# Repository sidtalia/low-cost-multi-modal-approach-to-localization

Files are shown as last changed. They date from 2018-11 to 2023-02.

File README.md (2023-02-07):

Associated paper: https://ieeexplore.ieee.org/abstract/document/8979000

If you find this work useful, please cite:
```
@inproceedings{talia2019multimodal,
  title={A multimodal approach for localization of Ackerman steering micro ground vehicles in bad GPS reception environments},
  author={Talia, Sidharth},
  booktitle={2019 3rd International Conference on Recent Developments in Control, Automation \& Power Engineering (RDCAPE)},
  pages={64--69},
  year={2019},
  organization={IEEE}
}
```

# Self-driving-car-STM-32

This project is the third iteration of my attempt at a mini self-driving car. It started as an imitation of the ArduRover project without all the fancy GUI. I started doing this practically on a dare, but quickly realized I absolutely enjoyed the point where cars met robotics. Personally, I am a petrolhead, but I also love making things work autonomously and this project feels like the perfect spot in the middle. While the title does say its a self driving car project, the focus is actually on aggressive driving. 



The above images show the first, second and third (current iteration) in that order. The first one had the connections hot-glued instead of soldered (yes). It has a come a long way since then.

The first and second versions were built on the Atmega328P and the third one on the STM32F103C8T6 (aka the 'blue pill'). In all these projects, my aim has been to keep the cost of the controller and hardware as low as possible. This does put a limitation on how much processing power I can have but that's really where all the fun is; to send a rocket to the moon with computational power less than that of a modern wristwatch.

Oh and by the way, only the rear wheels get power, i.e., its a rear-wheel-drive and rear-wheel-braking setup (imagine racing with a R.W.D car and using the hand brakes instead of normal brake pedals. Yikes!). This only makes the control problem more interesting.

Roadmap:
- [x] Outdoor relative localization (or odometry as most people like to call it)
- [x] Implement manual, partial manual and auto modes with failsafes
- [x] Trajectory generation and following
- [x] Preemptive braking to allow for faster speeds (Tested upto 8m/s on worn out tires. Will test again with new tires (normal medium soft compound)
- [x] Offline trajectory optimization given a set of waypoints (x,y) with a margin of adjustment and track width (WIP) 
- [ ] SONAR/LIDAR based obstacle avoidance for emergency braking (This part is taking a while because apparently cheap lidars don't work well in outdoor environments).
- [ ] Opponent detection using Object matching (may or may not be faster than object detection) (Jevois A33)
- [ ] Realtime trajectory update for overtaking (WIP)
- [ ] Designing overtaking policies (WIP. Currently learning about multi-agent navigation in UW's MUSHR project).

### About the project
The car can race around a track given a set of waypoints (already optimized for minimum laptimes). An offline optimizer does the job of optimization (Test Codes folder, waypoint.py). It can also act as a low level controller for higher level agents. The car can be given a point (X,Y,theta) relative to it's current location. Ideally, the higher level agent should give waypoints that do not force the car to go through an obstacle (that's kind of the point of having a higher level agent). The lower level controller takes care of figuring out the throttle and steering control for getting to a particular point.

### Odometry and localization
The localization is supposed to happen in open outdoor environments primarily using GPS data. I make the assumption that there is no exploitable feature in the environment. This is mostly because a system dependent on discernable features in the environment would not work as well in environments where there are none (CV techniques won't work in wide open parking lots). The user can always add their own way of localization and simply send the location data to the low level controller (the support for this will be incorporated if someone actually wants it). Most projects like these should be tested in wide open spaces for the sake of safety and so GPS based localization made the most sense as it is the most "generic" way of localization.



The odometry is obtained by fusing data from GPS, optical flow, IMU+compass and also from a simplistic model of the car's propulsion system, although the last method is kept as a last-resort under multiple sensor failures. The state estimator also exploits the non-holonomic constraints, using which it can get a speed measurement while the car is turning. Using multiple sources of information allows the car to operate with a high degree of accuracy (long term) when all the sensors are operating in peak condition and with an acceptable level of accuracy when one or two of the sensors are not in peak condition. The odometry assumes that the car is moving on a flat, horizontal plane (fair assumption for a car that has a ride height of 15 mm and is unlikely to go off-roading, however, the system can be extended to work on non-planar environments pretty easily).

Test for localization accuracy: https://youtu.be/GbBbyxaOqpI

Research paper for the same: https://ieeexplore.ieee.org/abstract/document/8979000
If this work is useful to you, please cite it! I'm a budding researcher and every citation goes a long way! :)

### Trajectory generation:
The trajectory is generated from given waypoints using parametric curves (3rd order Bezier curves). The motivation for me to use Bezier curves was to reduce computation and memory requirements as this codebase has to run on a tiny STM32F100 microcontroller.

### Waypoint generation:
The offline trajectory optimization takes in ordered waypoint regions, i.e., (X,Y, radius) as input arguments and finds the optimal (X, Y, heading) coordinates for the car to pass through such that the resulting trajectory would be optimal (what is considered "optimal" can be decided by the user). The cost function is comprised of a family of weighted potential fields (or sub-cost functions). These sub-cost functions are:

1) Total (absolute) curvature
2) The derivative of curvature
3) The second derivative of curvature
4) The overall length of the trajectory
5) C0 continuity between two consecutive sections
6) C2 continuity between two consecutive sections 
7) The sum of section-times (will be replaced with overall lap-time soon).

The weights for these sub-functions can be changed by the user. They are pre-multiplied by a normalizing factor so the weights can be adjusted relative to each other (a weight vector of [2,2,2,2] will have the same effect as a weight vector of [0.1,0.1,0.1,0.1]). The code for this is in /GCS/waypoint_optimizer.py. 



The next step is to make this less dependent on human input, like the work done here: https://github.com/a1k0n/cycloid (shoutout to a1k0n). 

### Control
The control is based on bezier curve(3rd order) based trajectory generation. There is also support for pre-emptive braking (more on that later).

The speed control uses an asymmetric non-linear controller. Big words? Here's a simpler explanation:
1) The car does not speed up and slow down in the same way; the response of the brakes is different from the response of the throttle, therefore there is asymmetry in the process being controlled.
2) The car does not speed up by the same amount for the same amount of change in throttle at different speeds, hence there is a non-linearity in the process being controlled.

(Note: I know that a system with a non-linear response is also by default asymmetric in response, but as I have specified above, the system is asymmetric beyond the general understanding of what it means to be asymmetric. The throttle controls the power to the wheels while the brake controls the force, in essence the system controls 2 completely different variables, leading to an asymmetric response.)

This means that in order to control the speed, I'd need a controller that compensates for both these problems and hence the big-words.
The steering control is an open + closed loop progressive P controller (progressive as in the gain increases with the error, like in a progressive spring). The combination of these 2 controllers allows the car to remain under control for the most part even without preemptive braking.

The control system can update the friction coefficient of the surface if it detects that the car is sliding when turning (by using optical flow data), and if it does enter a slide, it can handle itself ;)
GifMaker_20190831155907193

The system is also capable of preemptive braking, i.e., slowing down before the turn(as done in racing) instead of slowing down while turning.
Video link for preemptive braking :  https://www.youtube.com/watch?v=Ko5H_G4eCLo 
#### how preemptive braking is implemented: 
The car has a trajectory, it then finds the point of maximum curvature along that trajectory (upto the next checkpoint or waypoint) and determines maximum allowable speed for that curvature with some margin. The car then determines whether it should start slowing down for that point or not, on the basis of the deceleration required to hit that speed at that point. A more detailed discussion was done here (scroll down to the 5th last post which includes hand written notes): https://github.com/a1k0n/cycloid/pull/3

### Vision component: 
I have just started with computer vision please wait a couple of years.

### Ground control system and V2V communications:
The previous iterations did not have a GCS. This made debugging extremely hard as there wasn't an option of data recording or viewing the internal state of the controller in real time. The GCS in this work has the bare minimum features needed for debugging and is not on par with GCS's like Missionplanner or Qgroundcontrol, however, it gets the job done. The GCS allows me to record data that I could use for debugging as well as for finding flaws in the system. It can plot the position data from the car in real time.

The car is equipped with an Xbee pro (2.4GHz) and so is the GCS (GCS here can be your laptop). The actual purpose of the Xbee was not just for communication with the GCS for debugging and monitoring, but rather to allow multiple agents to communicate with each other, meaning that the car is V2X ready from the hardware's point of view. I got the inspiration to do this from a project I did last year under Celestini Program India at IIT-Delhi where I worked on ADAS coupled with V2V communication: https://github.com/Celestini-Lucifer/ADAS

# Note for potential users : 
The car will not operate without a GCS by default. This is for safety purposes and not for the sake of functionality. If the car were to operate without a GCS connection and only be in control of the user via radio control, there would be a single point of failure in communications. Adding the GCS-compulsion gives the system 2 independent points of failure. This also compulsorily limits the range of operation (which depends on the kind of transceiver used. For xbee pros, this range is ~80 meters, which is more than enough for doing experiments with a 1/10 scale car.)

The system has multiple failsafes (note that the car can be operated in auto modes without the transmitter, but it is advised to always keep a transmitter with you as a failsafe).
1) If the car goes outside the range of the GCS (Xbee, ~80 meters) the car will come to a halt. If the user wants to recover it, they have to move a 3 position switch on their Flysky Transmitter to the middle position for manual control (refer to the hardware folder for BOM). 
2) If the main controller (stm32f103c8t6) fails and stops producing appropriate pwm signals for the esc and servo, the secondary controller will take over and relay the control signals coming from the receiver directly to the esc and motor.
3) If the user feels that the main controller is misbehaving or not working as intended, they can flip switch D on their flysky fs-i6 (switch D on channel 6) to force the secondary controller to relay control signals directly from the receiver to the esc and motor.

## Photos of this project : 




## Building the project (in progress): 

(will update this as I build this project)

For the hardware specifications (including wiring specifications), 3d print files as well as 2 d drawings, go into the "hardware folder". 

For the back end libraries, go into the "libraries folder".

1) You will need : Arduino IDE (1.6.13 or better)

2) You will have to download the hardware files from : https://drive.google.com/file/d/1j8or7khmo2Z-QlrW-FHwhAybPbwVp9Ex/view?usp=sharing (its a slightly modified version of the original fork, I don't actually remember what changes I made but somehow the code after compilation takes 5 kB less memory) and unzip/extract it inside the "Arduino/hardware folder. You will also need to install the cortex M3 SAM board package in arduino, which can be installed easily through the boards manager in arduino IDE. Use this video for reference, the step of cloning the STM32 repository is replaced by downloading the zip and the rest remains the same : https://www.youtube.com/watch?v=MLEQk73zJoU&t=295s

The 'libraries folder' needs to go inside Arduino/libraries. The ino files need to go to wherever you store your sketches. Place the GCS folder where you keep your python files. The Baphomet code is for an Arduino Pro-Mini (5V, 16Mhz) and the Lucifer code is for the STM32F103c8t6. In the upload settings, set the CPU speed to overclocked (128Mhz) and upload method to serial.

### additional steps for Linux
Assuming you already have a functional installation of arduino (see here: https://www.arduino.cc/en/guide/linux )
You will probably face something that looks like this the first time you try to upload :
```
...../hardware/Arduino_STM32-master/tools/linux/serial_upload : error 13: Permission denied
```
just execute the following:
```
cd path/to/hardware/Arduino_STM32-master/tools/linux
sudo chmod +x *
```
and from within the same directory (path/to/hardware/Arduino_STM32-master/tools/linux)
```
cd stm32flash
sudo chmod +x *
```
now restart the arduino IDE and try uploading the code

### Common upload error:
```
Failed to init device.
stm32flash Arduino_STM32_0.9

http://github.com/rogerclarkmelbourne/arduino_stm32

Using Parser : Raw BINARY
Interface serial_posix: 115200 8E1

An error occurred while uploading the sketch
```
This happens when you forget to reset the stm32f103c8t6 (you have to push the reset button before the upload).
Again, watch this video for initial steps for stm32 bluepill https://www.youtube.com/watch?v=MLEQk73zJoU&t=295s

3) You will need Python
Python dependencies : 
Matplotlib,numpy, pyserial,scikit-learn :
```
pip3 install matplotlib
pip3 install numpy 
pip3 install pyserial
pip3 install scikit-learn
```

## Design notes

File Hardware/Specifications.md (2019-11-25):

# Hardware Specifications for this project

## The car : 
1) HPI sprint 2 (why? its a good balance between price and quality). I would suggest the "All aluminium upgrade".

2) ESC and motor : you're free to chose any ESC and motor combination but I like to run a 120 A ESC (hobbywing) and a (I use speedpassion but you can use any) 3500 kv sensored motor. (if you run the exact same hardware then you don't have to change a thing in the code).
3) Steering servo : SAVOX SC-1251MG . (any servo with equivalent or better torque and speed will work just fine. Any slower and you might face problems with oversteer).
4) Spur and pinion : 31 teeth pinion and 80-81 teeth spur (48 pitch both). if you use a different gearing ratio you'll have to calculate the maximum speed for your setup and put that number in the "CAR.h" file inside "libraries".
5) Drivetrain layout : RWD (this is to make space for the autopilot)
6) Suspension :
    1) Springs and dampers : standard HPI sprint 2 springs with 300 cst silicon oil all around.
    2) Steering geometry : 1 degree TOE-IN. (for stability at speeds). mount the steering links on the outer holes of the steering arms.
    3) Camber : Front = 0.5 or 0 degrees (Front end doesn't need that much camber). Rear = 2 degrees.
    4) Ride height : 25 mm all around. Think of this car as more of a road-rally sort of thing than a pure-bred racer.
7) Battery : 5000-6000 mAh 2S lipo. C rating may or may not matter depending upon your use case. I use 70C batteries from turnigy trackstar.

## The autopilot : 
1) The designs (obviously)
2) 1 x STM32F103C8T6 (if you get the CBT6 that works too) and 1 x Pro mini.
3) 1 x MPU9250.
4) 1 x ADNS3080 optical flow sensor.
5) 1 x Ublox M8N GPS (no config required, the code will do the config automatically for you).
6) 1 x Jevois A33 (optional) and a usb mini-b male adapter.
7) 2 x Xbee Pro with Xbee pro adapter (one for the car and one for your computer).
8) 1 x pwm to ppm converter (like the one used for Ardupilot).
9) 1 x Flysky Fs-i6 (or equivalent). Put switches C and D on channels 5 and 6
10) 1 x 5V/5A BEC (the one that you get from bang-good is just fine. It can actually only handle 3A without a voltage sag, but you can push it to 5. We won't actually need 5 A at all. We'll need ~1-1.2 A (this includes the current consumed by the jevois camera. If you're not using the jevois camera, the current consumption will be much lower, however I would still recommend using a separate BEC).
11) 4 x LEDs taken out from a computer mouse (please do not use a standard red LED. Just take the LED out from an old mouse. 
12) 1 x dot board/Zero pcb, single core wires, solder, male headers.
13) I might add more things for obstacle avoidance later. Right now I m considering the use of the camera itself to detect obstacles or run image segmentation

# Putting it together : (images will be up soon)
1) The chassis and chassis brace drawings are .dwg files because it has no 3d features and you can do a cnc(1.5 mm offset) cut. If someone asks for it I will upload an stl file if you want to 3d print it
2) The LED holder sits on top of the chassis above the slot. The holes have been cut into the chassis.
3) the chassis brace has holes for mounting the container base. mount the container on the chassis brace before adding any components to the autopilot.
4) the MPU is to be situated at the converging end of the container. The optical flow is placed in the raised slot. The GPS is placed on the container top behind the jevois camera.
5) the xbee is situated near the motor, so is the BEC and the pro mini.
6) The MPU is attached to pins B6 (SCL), B7 (SDA).
7) The Optical flow is attached to pins PA4 (NSS) PA5 (SCK) PA6 (MISO) PA7 (MOSI) PB0 (RESET)
8) The GPS is attached to PA2 (Tx, Rx of gps connected here) PA3 (Rx, Tx of gps connected here)
9) The Xbee is connected to PA9, PA10. Create a 6 pin male header that can accept an FTDI converter and connect the Xbee (and only the xbee) with jumper wires that can be removed later).
10) The Jevois is connected to pins PB11 (white wire), PB10 (yellow wire).
11) The extend a wire from pin PA8, PA11 to pins 3 and 4 of pro mini. These are servo and ESC wires.
12) Connect the PPM encoder to pin 9 of pro mini. solder a wire from PA0 to pin 9 of pro mini.

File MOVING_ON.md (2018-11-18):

# Why I moved on from the Arduino Pro Mini:

## Why improve the hardware?

Problems with Arduino Pro Mini:

1) Not enough UART ports (required for communication with GCS and a higher level system like idk a raspi or a jevois camera)

2) Not enough processing speed to maintain the same 400Hz state-estimation frequency with any added features (like sensor health checks). I was shaving off like 10-15 us per function minimum just to meet the requirements (although this did force me to come up with rather ingenious approximations which I have carried over to this project, so if you use my "math" functions (in the SIDMATH.h header) you can forget worrying about execution time of your algorithms- Its not a full blown math library because it isn't meant to be. It just includes some functions that I used very often like sin and cos my approximations are pretty close and have a worst case execution time which is 1/3rd (if i remember correctly) of the time taken by arduino's sin and cos. ).

Problems with previous layout of hardware:

1) The optical flow sensor was outside of the boundary of the car(behind the car) this caused there to be an unwanted cg offset + ugliness. The optical flow sensor now sits at the center of the car (at the cost of front wheel power. The car is now RWD).

2) Everything was connected by jumper wires. Yes. Really. In the new version, everything is soldered directly. 

Problem with previous hardware in general (this doesn't come under the above 2 categories) : 

1) The last and final crash of my previous iteration happened on July 22nd 8:30 AM. It happened because the MPU got disconnected mid-communications, which locked up the I2C line, producing a race-around condition. Due to this, the car could no longer be sent into a failsafe as it had gone into a lockout state. The car went at 7 m/s into a wall at an oblique angle, taking out the right front suspension.
For this reason I decided to put 10k resistors between SCL,SDA and VCC to prevent the race-around condition and instead of having just the main controller, have a slave controller that acts as a gateway between the car's hardware and the main controller, so that in case the main controller goes haywire, the slave controller can still shut the car down. How do I know this slave controller won't go into some lockout mode of it's own? I have tested the back end for it over 2 years and it has never failed (since it only uses interrupts and servo library and nothing else). It's sole job is to make sure that the car never goes completely out of control. (I am still on the fence about this though).

So whats the alternative? the STM32F103C8T6 (surprise surprise!) (a.k.a. the blue pill). The blue pill has 3 UARTs, 2 SPIs and 2 I2Cs (although I only use 1 I2C and 1 SPI port in this project, its nice to have options), 20kb of sram, 64 kb of flash memory (compared to 2 kb of sram and 32 kb of flash memory on mini pro), and a clock speed of 128MHz (after overclocking, which can be done from within the arduino IDE itself). Going from a Pro mini to the blue pill feels like going from a handgun to a bazooka.

Why improve the code? 
The right question would be, why not? The previous version had certain (kidding, a lot of) flaws like lack of modularity (each sub-module should be able to function somewhat on it's own and not be dependent on some other module entirely. If you look at my previous code, just about all variables are global. It gets hard even on the person who created it after a while (this is why object oriented programming is used kids) ) as well as misplaced functionalities (like incrementing waypoint index in the code block that is supposed to control the steering and throttle. Yes. Really. (cut me some slack I m still learning) ). 

In this version, I wrote back end libraries for just about everything (FYI this is my first time writing back end libraries) from IMU to the communication systems, so that I could divide things into sub-modules. This greatly cleans up the main code (though it's still not that clean). However, everything related to AHRS, from getting sensor data to calculating AHRS happens in the same library so that all the helper functions that could be used are in the same file.

If you know how to write code for a GCS in python, please create an issue and let me know, I need some help there. I can't seem to integrate google maps into this. Till then, Waypoints will be marked by driving the car to those waypoints in manual mode.

## Have I forsaken Arduino? 
No. The code is still compiled by the Arduino IDE. The main code that runs the car is still written in Arduino IDE (bite me). Why not just work with pixhawk (Ardupilot)? 

1) I am too dumb to understand what they're doing there. I am just not up there yet. So its better that I do not fiddle with things I do not understand.

2) I am trying to learn these things on my own. If I use the Ardupilot backend I will never really understand how these things work and what you need to take care of (corner cases, exceptions etc). 

3) If I have my own system, its easier for me to integrate new things into it since I don't have to comply to standards set by someone else. While standards are very useful at the professional level, they can slow down the process of testing and between my undergrad studies, academic projects, research papers and this, I do not have the time to go through these things like a professional.

4) If you wanna create a project using arduino supported mcus, you install the Arduino IDE and maybe some back end support (like back end support for STM32 controllers) which is also downloaded from within the Arduino IDE. Its super simple and you can get started with doing actual work. If you wanna create a project using pixhawk and you're on Windows, may god help you. 

Basically we need something like Multi-Wii but for r/c race cars instead of drones and we need it to be somewhat competitive against the apm rover. We also need it to be a bit more focused on racing, which means a bit more focus on the driving dynamics of the car (which AFAIK the apm does not really have since they simply minimize the angle difference between the direction where they wanna go and where they are going right now, which is fine and even required for WP missions but for racing you need the car to follow a smooth trajectory).

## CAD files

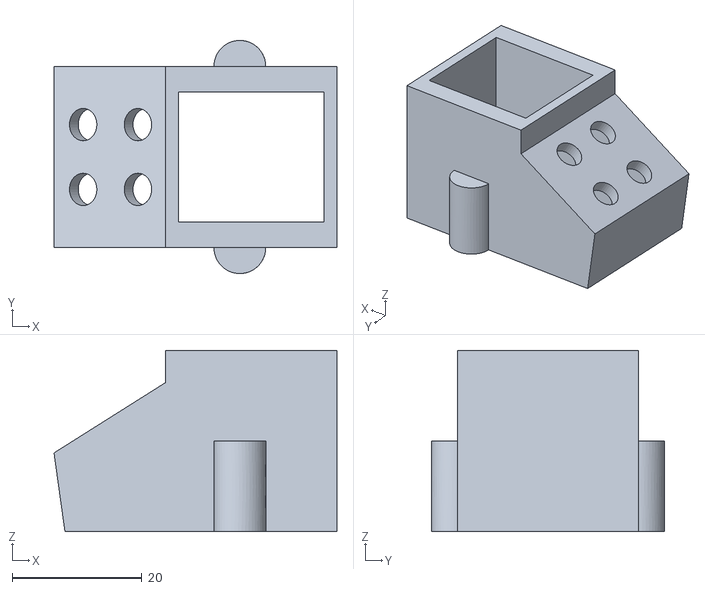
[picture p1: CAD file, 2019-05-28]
Hardware/LED_holder_proto_4.stl
43.7 x 36.0 x 28.0

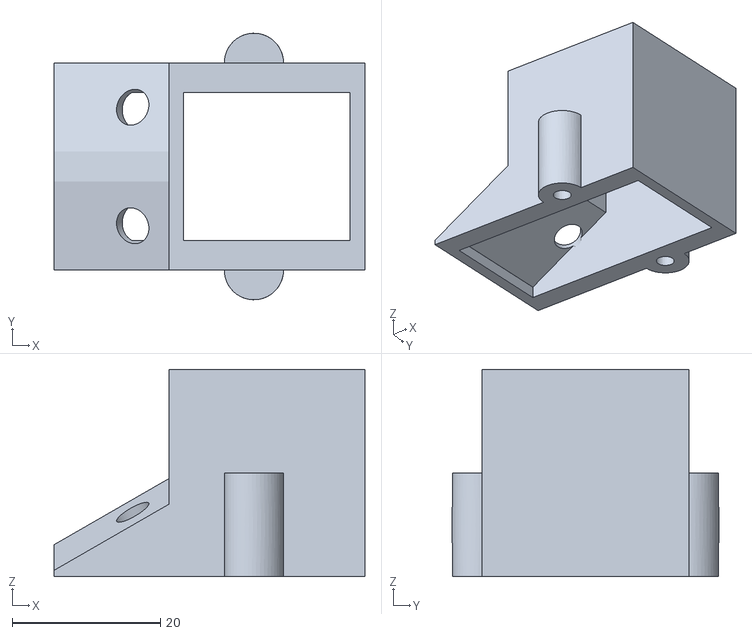
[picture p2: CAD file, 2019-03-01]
Hardware/LED_holder_new.stl
42.0 x 36.0 x 28.0

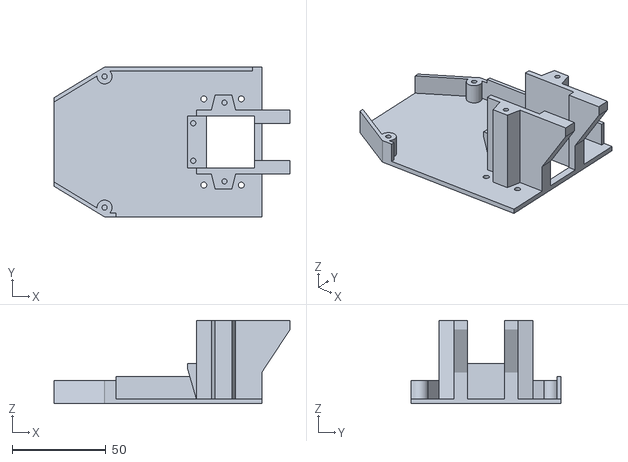
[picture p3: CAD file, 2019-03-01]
Hardware/container_base_new.stl
126.0 x 80.0 x 44.5

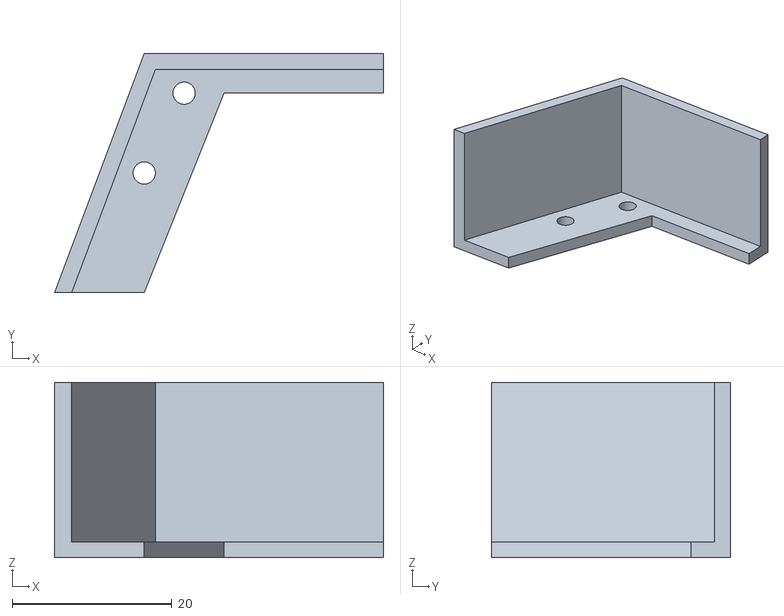
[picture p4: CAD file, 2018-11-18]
Hardware/Dust_gaurd_right.stl
41.2 x 30.0 x 22.0

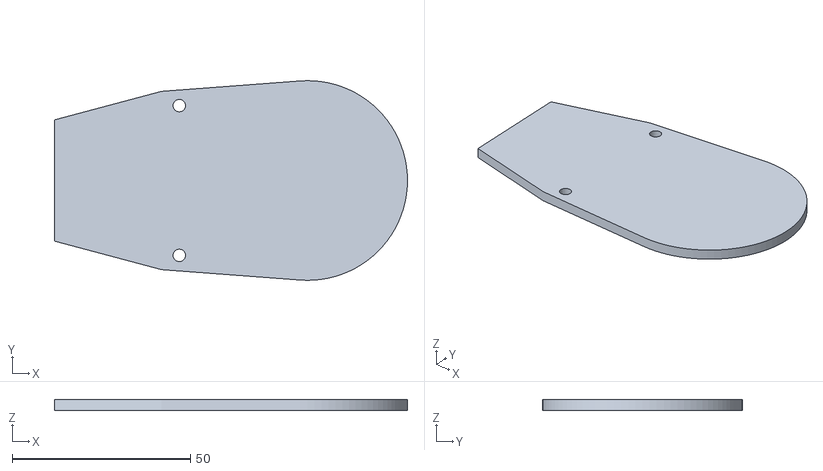
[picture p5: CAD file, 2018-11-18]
Hardware/container_jevois_gps.stl
99.0 x 56.0 x 3.00

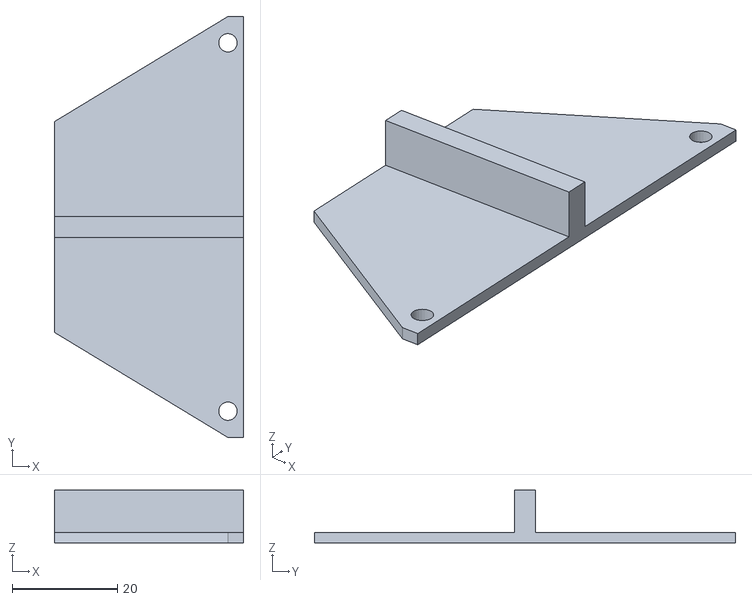
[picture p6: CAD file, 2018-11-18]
Hardware/container_top.stl
36.0 x 80.0 x 10.0

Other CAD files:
Hardware/chassis_design_updated_7_Aug_2019.dwg
Hardware/Dust_gaurd_left.stl
Hardware/chassis_brace.dwg
Hardware/modified_chassis_New.dwg

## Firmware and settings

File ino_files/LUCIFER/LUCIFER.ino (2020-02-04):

//You might observe some inconsistency between tabs and spaces between arduino code and the header file code.
//If that is a problem for you then you are free to edit the code yourself. I don't have the time to be concerned 
//with formatting as long as the code remains understandable.

//choose the 128MHz overclocked setting for compilation.

//If you want to cross check the time taken by any function, here is some help:
//in floating point, each multiplication takes 0.61us, each addition/subtraction takes 0.481 us, each division 2.14us
//in integer, divide the above numbers by 2 (roughly speaking). This gives a decent estimate of execution time. 
//The cycle time is constrained to 2500us. While its possible to run it down to 1250us without breaking a sweat, it would sacrifice system safety checks
//and re-initialization processes (say for example the MPU is somehow shut-off by chance. it takes about 470 us to re-initialize it).
#include"MPU9150.h"
#include"OPFLOW.h"
#include"GPS_NAV_PVT.h"
#include"MEMORY.h"
#include"INOUT.h"
#include"SIDMATH.h"
#include"COMS.h"
#include"STATE.h"
#include"CAR.h"
#include"PARAMS.h"
#include"TRAJECTORY.h"
#include"COMPANION.h"//CHANGED

MPU9150 marg;
OPFLOW opticalFlow;
GPS gps;
STATE car;
GCS gcs;
trajectory track;
controller control;
JEVOIS jevois; //CHANGED

bool GPS_FIX;
byte MODE = MODE_STANDBY;
byte message;
float inputs[8];
int16_t num_waypoints=0;
int16_t point = 0;
int16_t sentinel = 0;
bool circuit = false; //
bool car_ready = false;
float dest_X,dest_Y,slope;

coordinates *c;

void setup() 
{
//  initialize all coms
  Serial.begin(COM_BAUD);
  Serial1.begin(GPS_BAUD);
  Serial2.begin(JEVOIS_BAUD);
  SPI.begin();
  Wire.begin();
  Wire.setClock(400000);  //start initializing driver code
  delay(1000);
  IO_init();
  set_Outputs(0,0);
  
  marg.initialize();
  opticalFlow.initialize();
  opticalFlow.caliberation(ride_height,0.0f ); //ride_height is stored in the param's header
  gps.initialize();

  int16_t A[3],G[3],M[3],T,gain[3];
  if(!check_memory()) //if there are no offsets in the memory
  {
    bool avail = false;
    long check_time = millis();
    while(!avail)
    {
      avail = gcs.Get_Offsets(marg.offsetA, marg.offsetG, marg.offsetM, marg.offsetT,marg.axis_gain);
      if(avail || millis()-check_time>10000)
      {
        break;
      }
    }
    if(avail)//if GCS already has offsets
    {
      marg.getOffset(A,G,M,T,gain);
      store_memory(0, A,G,M,T,gain);
    }
    //if GCS has no offsets and we don't have the offsets
    else
    {
      gcs.Send_Calib_Command(1); //let GCS know we are doing calib
      delay(2000);
      marg.gyro_caliberation();
      //keep the car still, rotate it 180, keep the car still again, rotate 180.
      gcs.Send_Calib_Command(2);
      delay(2000);
      marg.accel_caliberation();

      gcs.Send_Calib_Command(3);
      delay(2000);
      marg.mag_caliberation();

      gcs.Send_Calib_Command(4);
      
      marg.getOffset(A,G,M,T,gain);
      store_memory(0, A,G,M,T,gain);
      
      gcs.Send_Offsets(marg.offsetA, marg.offsetG, marg.offsetM, marg.offsetT, marg.axis_gain); //send new found offsets to GCS
    }
  }
  else
  {
    read_memory(0, A,G,M,T,gain);
    marg.setOffset(A,G,M,T,gain);
    gcs.Send_Offsets(marg.offsetA, marg.offsetG, marg.offsetM, marg.offsetT, marg.axis_gain); //send new found offsets to GCS
  }
  marg.Setup();
  
  gps.localizer();//get initial location
  long timeout = millis();
  do //wait till we get a GPS fix
  {
    gcs.Send_State(MODE, gps.latitude, gps.longitude,gps.latitude,gps.longitude, marg.V, marg.mh, marg.pitch, marg.roll, marg.Ha, opticalFlow.P_Error, 0, marg.mh_Error, marg.V_Error, 0,gps.Hdop,0);
    if(gps.Hdop>1000)//if gps is unavailable, skip.
    {
      delay(100);
      break;
    }
  }
  while(gps.fix_type()<2 && millis() - timeout < FIX_TIMEOUT );
//  if(gps.fix_initial_position()&&0) //get initial coordinates
  if(0)
  {
    GPS_FIX = 1;
  }
  else
  {
    GPS_FIX = 0;
    delay(100);
    gps.localizer(); //use latest position from gps as a starting point.
  }

  car.initialize(gps.longitude, gps.latitude, gps.Hdop, marg.mh, 0, marg.Ha);
  
}

unsigned long timer,time_it;
unsigned long T,benchmark;
bool reflect_WP = false;
float dummy;
int16_t jevois_message;
float jevois_X,jevois_Y;

void clear_wp()
{
  num_waypoints = 0;
  point = 0;
  sentinel = 0;
  circuit = 0;
  car_ready = false;
  delete[] c; //clear all waypoints
}

void loop() 
{
  timer = micros();//this is to ensure that the cycle time remains constant at 2500us. How do I know it's not exceeding that limit? 
                    //I unit test each of the functions to check how much time they take to execute.
  //================GET SENSOR DATA================
  control.get_model(marg.encoder_velocity); //comment out if not using output throttle signal as a rough speed estimate
  marg.compute_All(); //get AHRS (and Velocity as well) from IMU. 980us, has failsafe in case sensor is reset somehow
  
  marg.get_Rotations(opticalFlow.omega); //transfer rates of rotation
  opticalFlow.updateOpticalFlow(); //update optical flow 150us
  if(opticalFlow.failure)
  {
    timer = micros();
  }
  gps.localizer(); //update gps. 12us
  //till here it takes 180us, total at 1170us
  //================SENSOR FUSION===================
  car.state_update(gps.longitude, gps.latitude, gps.tick, gps.Hdop, gps.gSpeed, gps.Sdop, gps.headMot, gps.headAcc,
                  marg.mh, marg.mh_Error, marg.yawRate, marg.heading_drift, marg.Ha, marg.V, marg.V_Error,
                  opticalFlow.X, opticalFlow.Y, opticalFlow.V_x, opticalFlow.V_y, opticalFlow.P_Error, opticalFlow.V_Error,marg.encoder_velocity); //I know i could've just passed the gps, marg and optical
                              //flow objects but then the state library would become dependent on these libraries and for some unkown reason I want to keep it a bit more generic
  marg.Velocity_Update(car.Velocity,car.VelError,car.AccBias);//pass the corrected velocity back to marg where it gets low pass filtered too.
  
  control.feedback(car.Velocity,car.VelError,opticalFlow.V_Error);//giving feedback to the car's model for making the machine learn the parameter(s) of the model
//transfer the bias. this is pretty much the reason why the update function does not take arguments by reference
  //till here it takes 120us, total at 1330us
  //================HANDLE COMMUNICATIONS================

  message = gcs.check();//automatically regulates itself at 10Hz, don't worry about it
  if(reflect_WP)//if waypoints are to be sent back, this remains true
  {
    reflect_WP = !(gcs.Send_WP(c[point].X,c[point].Y,c[point].slope,point)); //this function will return true when waypoints have been sent back
  }
  else //this is for the general case
  {
//    gcs.Send_State(MODE, double(car.X), double(car.Y),gps.longitude, gps.latitude, car.Velocity, marg.mh, marg.pitch, marg.roll, 
//                  inputs[7], opticalFlow.SQ, car.PosError_tot , marg.mh_Error, car.VelError, T,gps.Hdop); //also regulated at 10Hz
//      gcs.Send_State(MODE, double(car.X), double(car.Y),double(track.X_max),double(track.Y_max),track.C[1],track.braking_distance,marg.mh,0,
//                    car.Velocity, opticalFlow.SQ, car.PosError_tot , marg.mh_Error, 3.15, benchmark,gps.Hdop);
//    gcs.Send_State(MODE, double(gps.VelNED[1]),double(gps.VelNED[0]) ,gps.longitude, gps.latitude, gps.gSpeed, marg.mh, marg.pitch, marg.roll, 
//                  gps.headVeh, gps.headMot, car.PosError_tot , marg.mh_Error, 3.16, T,gps.Hdop); //also regulated at 10Hz
    gcs.Send_State(MODE, double(car.X), double(car.Y),gps.longitude, gps.latitude, car.Velocity, marg.mh, marg.pitch, marg.roll, 
                  marg.heading_drift, opticalFlow.SQ, car.PosError_tot , marg.mh_Error, car.VelError, T,gps.Hdop, jevois.rec_status()); //also regulated at 10Hz
  }
  if(gcs.get_Mode()!=255)//255 is condition for no message received yet.
  {
    MODE = gcs.get_Mode();
  }
  
  get_Inputs(inputs); //get inputs from r/c receiver
  if(gcs.failsafe)//if gcs has shutdown for some reason, fallback on the transmitter.
  {
    if(inputs[5] <= 1100)
    {
      MODE = MODE_STANDBY;
    }
    if(inputs[5] > 1100 && inputs[5] < 1600)
    {
      MODE = MODE_MANUAL;
    }
    if(inputs[5] > 1600)
    {
      MODE = CRUISE;
    }
    if(inputs[2]<1000)//if even the transmitter is off, then inputs[2] will have a value of less than 1000.
    {
      MODE = MODE_STANDBY;
    }
  }

  if(message == SET_ORIGIN_ID)//this is for resetting the position
  {
    car.initialize(gps.longitude, gps.latitude, gps.Hdop, marg.mh, 0, marg.Ha);
  }
  
  if(message == CALIB_ID)//recalculate offsets
  {
    int16_t A[3],G[3],M[3],gain[3],T;
    gcs.Send_Calib_Command(1); //let GCS know we are doing calib
    delay(2000);
    marg.gyro_caliberation();//keep the car still, rotate it 180, keep the car still again, rotate 180.
    gcs.Send_Calib_Command(2);
    delay(2000);
    marg.accel_caliberation();
    
    marg.getOffset(A,G,M,T,gain);
    store_memory(0, A,G,M,T,gain);
    
    gcs.Send_Offsets(marg.offsetA, marg.offsetG, marg.offsetM, marg.offsetT,marg.axis_gain); //send new found offsets to GCS
    timer = micros(); //reset timer  
  }

  if(message == WP_ID)//if waypoint message is received
  {
    reflect_WP = true; //we'll have to reflect the waypoints
    if(num_waypoints==0)//if we have not initialized the waypoints yet
    {
      num_waypoints = gcs.msg_len;//for WP, the msg_len is not the length of the received packet, its the number of waypoints that will be given to the car in totality.
      c = new coordinates[num_waypoints];
      point = 0;//initialize point.
    }
    if(point < num_waypoints && num_waypoints !=0)
    {
      float dummy_X,dummy_Y,dummy_Slope;
      gcs.Get_WP(dummy_X, dummy_Y,dummy_Slope,point); //get the coordinates
      c[point].X = dummy_X;
      c[point].Y = dummy_Y;
      c[point].slope = dummy_Slope;
      c[point].calcLatLon(car.iLon, car.iLat); // calculate lat lon just in case
      if(point == num_waypoints-1)
      {
        if( check_loop(c[0],c[point]) ) //check if first and last points are within 1/2 a meter range
        {
          circuit = true;
          c[point].copy(c[0]);
        }
//        track.generate_Slopes(c,num_waypoints, circuit); // generate the slopes! happens only once so I reset the timer 
        track.get_fixed_maximas(c, num_waypoints, circuit);
        dest_X = c[0].X;
        dest_Y = c[0].Y;
        slope  = c[0].slope;
        car_ready = true;
        sentinel = 0;
        timer = micros();
      }
    }
    else
    {
      gcs.Send_Calib_Command(5);
    }
  }
  if(message == CLEAR_ID && num_waypoints!=0)
  {
    clear_wp();
  }
  //========COMPANION CODE HERE=========
  jevois_message = jevois.check();
  if(jevois_message==STATE_ID)
  {
    jevois.get_data(jevois_X,jevois_Y);
  }
  jevois.handle_Recording(message); //check if the message asks to start/stop recording and then handle it
  jevois.Send_State(MODE, car.X, car.Y, marg.mh, dest_X, dest_Y, slope, marg.pitch, marg.roll, marg.yawRate, car.Velocity);//CHANGED
  //====================================
  
  if( distancecalcy(car.Y, dest_Y, car.X, dest_X,0) <= WP_CIRCLE && num_waypoints!=0 && car_ready)//checking if waypoint has been reached
  {
    sentinel++;
    if(circuit)
    {
      sentinel = sentinel%num_waypoints;
      dest_X = c[sentinel].X; //TODO : maybe just pass the object of the coordinate instead of transfering all the values manually.
      dest_Y = c[sentinel].Y;
      slope = c[sentinel].slope; 
    }
    else
    {
      sentinel = min(sentinel,num_waypoints-1);
      if(sentinel == num_waypoints-1)
      {
        clear_wp();
      }
      else
      {
        dest_X = c[sentinel].X; //TODO : maybe just pass the object of the coordinate instead of transfering all the values manually.
        dest_Y = c[sentinel].Y;
        slope = c[sentinel].slope; 
      }
    }

  }

  if(opticalFlow.failure)
  {
    MODE = MODE_STOP; //this is to ensure the car does not rocket itself into a wall due to an electronic failure on the optical flow's end, which is not highly likely but has happened some times.
  }
  if( (MODE == CRUISE || MODE == LUDICROUS) && point == num_waypoints-1 && num_waypoints!=0 )//autonomous modes. The paranthesis are important! the conditions need to be clubbed together
  {
    time_it = micros();
    track.calculate_Curvatures(car.Velocity, car.X, car.Y, car.heading, dest_X, dest_Y, slope ); 
    track.confirm_maxima_priority(c[sentinel], track.X_max, track.Y_max, track.C[1], track.braking_distance);
    benchmark = micros()-time_it;
    control.driver(track.C, track.braking_distance, car.Velocity,car.drift_Angle, marg.yawRate, marg.La, marg.Ha, MODE, inputs); //send data to driver code. automatically maintains a separate control frequency.
    dummy = track.braking_distance;
  }
  else if(MODE == MODE_PARTIAL || MODE == MODE_MANUAL || MODE == MODE_STOP || MODE == MODE_STANDBY || MODE==MODE_CONTROL_CHECK)//manual modes
  {
    float dum[] = {0.0,0.0};//dummy
    control.driver(dum, 1000, car.Velocity,car.drift_Angle, marg.yawRate, marg.La, marg.Ha, MODE, inputs);
  }
  else
  {
    float dum[] = {0.0001,0.0001};//dummy
    MODE = MODE_STANDBY;
    control.driver(dum, 1000, car.Velocity,car.drift_Angle, marg.yawRate, marg.La, marg.Ha, MODE, inputs);
  }
  if(micros()-timer > dt_micros)//in case the execution time exceeds loop time limit
  {
    gcs.Send_Calib_Command(5);
  }
  
  T = max(micros()-timer,T);
  while(micros()-timer < dt_micros ); //dt_micros is defined in PARAMS.h
}

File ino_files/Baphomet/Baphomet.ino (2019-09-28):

#include<Servo.h>

volatile unsigned long timer[5];
volatile byte last_channel[6], tick = 0;
volatile int input[11]={1500,1500,1500,1500,1500,1500,1500,1500,1500,1500,1050};
volatile int delT;
volatile bool servoWrite = false,takeover = false,ultrasonic = false;
long failsafe,usr_timer;

Servo motor, steer, usr;

void setup()
{
  PCICR |= (1 << PCIE0);   
  PCMSK0 |= (1 << PCINT0); //8
  PCMSK0 |= (1 << PCINT1); //9
  PCMSK0 |= (1 << PCINT2); //10
  PCMSK0 |= (1 << PCINT3); //11
  pinMode(3,INPUT);
  pinMode(4,INPUT);
  usr.attach(5);
  Serial.begin(38400);
}


void serialprint()
{
  Serial.print(input[0]);Serial.print("||");
  Serial.print(input[1]);Serial.print("||");
  Serial.print(input[2]);Serial.print("||");
  Serial.print(input[3]);Serial.print("||");
  Serial.print(input[4]);Serial.print("||");
  Serial.print(input[5]);Serial.print("||");
  Serial.print(input[6]);Serial.print("||");
  Serial.print(input[7]);Serial.print("||");
  Serial.print(input[8]);Serial.print("||");
  Serial.print(input[9]);Serial.print("||");
  Serial.println();
}


void fucc()
{
  digitalWrite(3,LOW);
  digitalWrite(4,LOW);
}
  
void loop()
{
  long timer = micros();
  if(input[2] < 1000)
  {
    fucc();
    takeover = false;
    motor.writeMicroseconds(1500);
    steer.writeMicroseconds(1500);
  }
  else if((takeover && !(input[2]<1000))or input[4]>1500)//SWITCH 5 IS THE KILL SWITCH.
  {
    pinMode(11,OUTPUT);
    pinMode(10,OUTPUT);
    motor.writeMicroseconds(input[2]);
    steer.writeMicroseconds(input[0]);
    Serial.println("got here");
  }

  if(servoWrite)
  {
    failsafe = millis();
    servoWrite = false;
//    takeover = false;
  }
  if(millis() - failsafe > 1000&&takeover==false)
  {
    takeover = true;
    motor.attach(4);
    steer.attach(3);
    Serial.print("in");
  }

  if(ultrasonic)
  {
    usr_timer = millis();
    ultrasonic = false;
  }
  if(millis()-usr_timer < 200)
  {
    usr.writeMicroseconds(input[10]);
  }
  else
  {
    usr.writeMicroseconds(1050);
  }
  
  while( micros() - timer < 20000);
}

ISR(PCINT0_vect)
{
  timer[0]=micros();
  //channel 1 ----
  
  if(last_channel[0]==0 && PINB & B00000010) //makes sure that the first pin was initially low and is now high
  {                                         //PINB & B00000001 is equivalent to digitalRead but faster
    last_channel[0] = 1;
    delT=timer[0]-timer[1];          
    if(delT>3000)
    {
      tick=0;
    }
    else
    {
      input[tick++] = delT;
    }
    timer[1]=timer[0];
  }
  else if(last_channel[0]==1 && !(PINB & B00000010))
  {
    last_channel[0]=0;
  }
  //channel 2---                  
  if(last_channel[1]==0 && PINB & B00000100) //makes sure that the first pin was initially low and is now high
  {                                         //PINB & B00000001 is equivalent to digitalRead but faster
    last_channel[1]=1;
    timer[2]=timer[0];          
  }
  else if(last_channel[1]==1 && !(PINB & B00000100))
  {
    last_channel[1]=0;
    input[8]=timer[0]-timer[2];
    servoWrite = true;
  }
  
  //channel 3-- 
  if(last_channel[2]==0&& PINB & B00001000) //makes sure that the first pin was initially low and is now high
  {                                         //PINB & B00000001 is equivalent to digitalRead but faster
    last_channel[2]=1;
    timer[3]=timer[0];          
  }
  else if(last_channel[2]==1 && !(PINB & B00001000))
  {
    last_channel[2]=0;
    input[9]=timer[0]-timer[3];
    
  }
  //ULTRASONIC CHANNEL
  if(last_channel[3]==0&& PINB & B00000001) //makes sure that the first pin was initially low and is now high
  {                                         //PINB & B00000001 is equivalent to digitalRead but faster
    last_channel[3]=1;
    timer[4]=timer[0];          
  }
  else if(last_channel[3]==1 && !(PINB & B00000001))
  {
    last_channel[3]=0;
    input[10]=timer[0]-timer[4];
    ultrasonic = true; // set the flag
  }
}

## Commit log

2018-12-14 corrected semantic error.
    correction : was using TIMER4 instead of TIMER 1 for driving pwm outputs. :P
2019-01-14 dealing with single IMU
2019-03-04 Create BOM
2019-03-04 Update BOM
